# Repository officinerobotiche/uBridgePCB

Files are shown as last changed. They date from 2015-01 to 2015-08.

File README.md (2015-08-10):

# Officine Robotiche uBridge PCB
**The first DC motor board in 4cm X 4cm** - PCB boards for uBridge

This is a project in development by [Officine Robotiche] team.

###Join on open firmware project [uNAV.X](https://github.com/officinerobotiche/uNAV.X)!!!

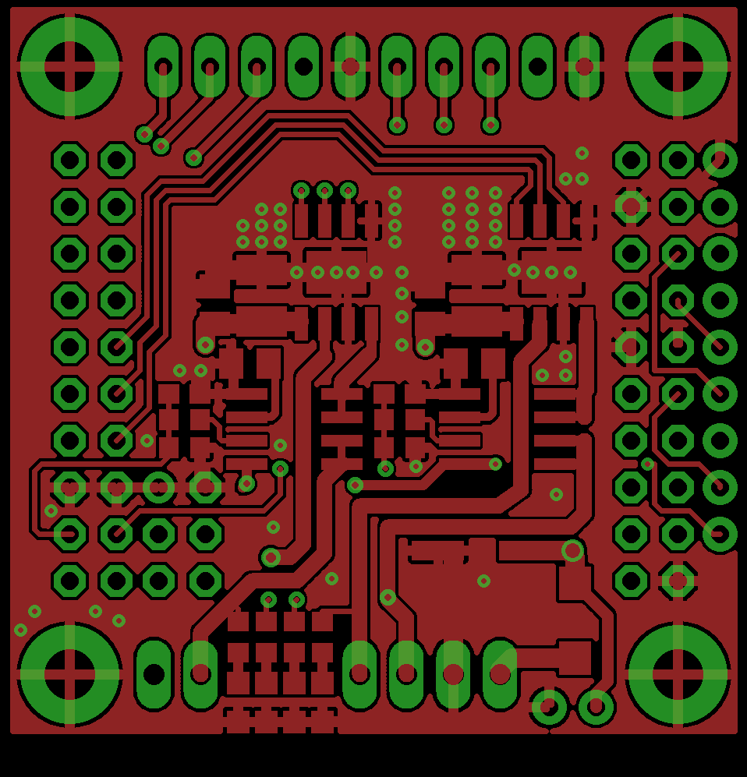
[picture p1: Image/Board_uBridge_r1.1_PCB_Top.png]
uBridge PCB Top

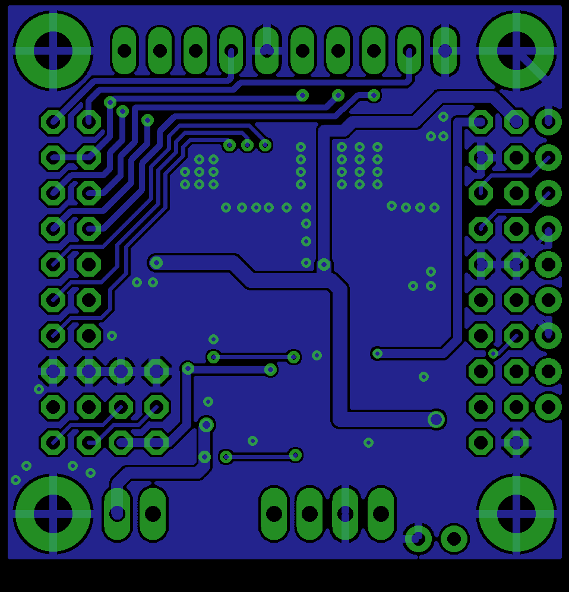
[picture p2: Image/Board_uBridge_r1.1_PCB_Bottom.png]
uBridge PCB Bottom

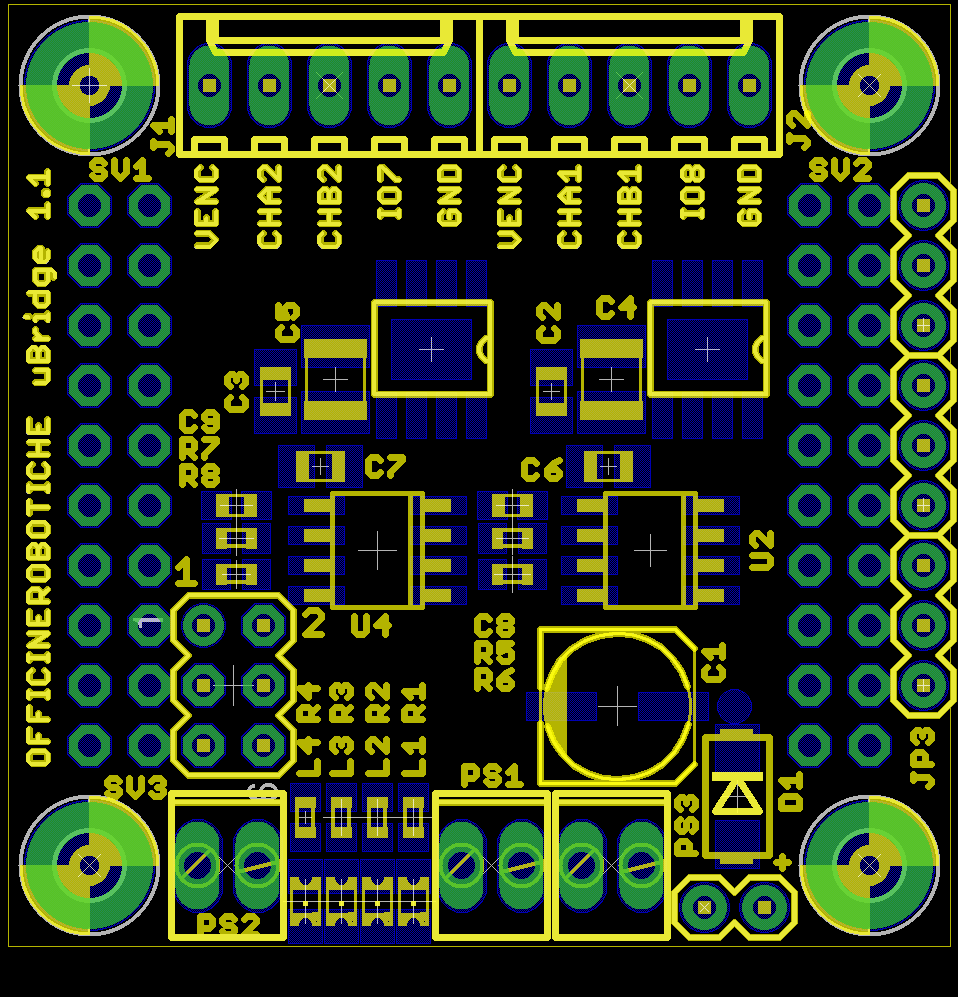
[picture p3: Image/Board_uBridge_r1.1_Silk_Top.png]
uBridge Silkscreen Top

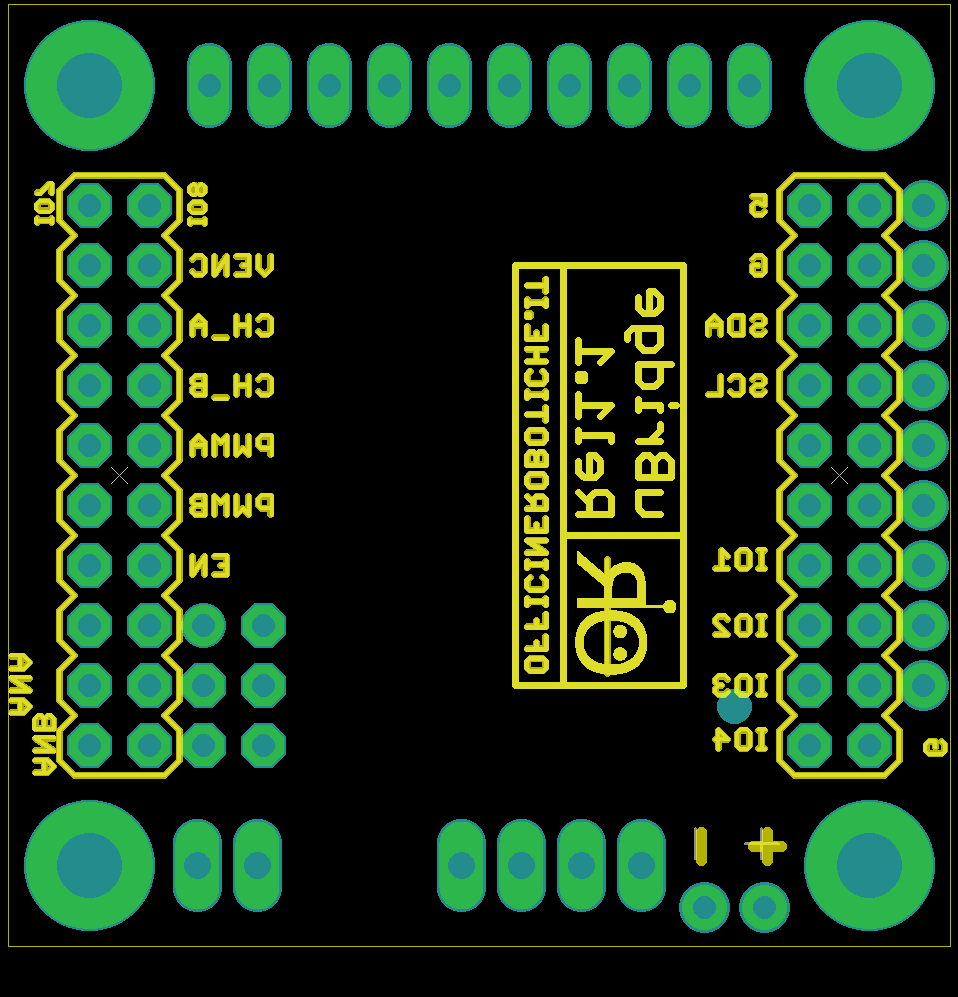
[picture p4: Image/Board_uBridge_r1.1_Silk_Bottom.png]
uBridge Silkscreen Bottom


# Hardware features
- 2 x A4950 Full-Bridge DMOS PWM Motor Driver
  - Up to 3,5A and 40V input ( limited at 23V if used with uNav )
  - Short circuit protected
  - Over Temperature protected
- 2 x ACS712 Hall Effect-Based Linear Current Sensor IC
  - ±5A Full-Scale input Range with 185mV/A variation
  - 2,5V output @ 0.0A
- 2 connector for Encoder with Gnd, Vcc, ChA, ChB, Chz signal.
- 4 LED on outupt of H-Bridge.
- Protection diode on input.
- size: 4cm x 4cm uNav stackable.
- Matrix board with holes 2.54mm compliant.

# Available Shields
- [uNav](https://github.com/officinerobotiche/uNAVPCB)
- [uMatrix](https://github.com/officinerobotiche/)

[Officine Robotiche]:http://www.officinerobotiche.it/
[Logo]:http://2014.officinerobotiche.it/wp-content/uploads/sites/4/2014/09/ORlogoSimpleSmall.png

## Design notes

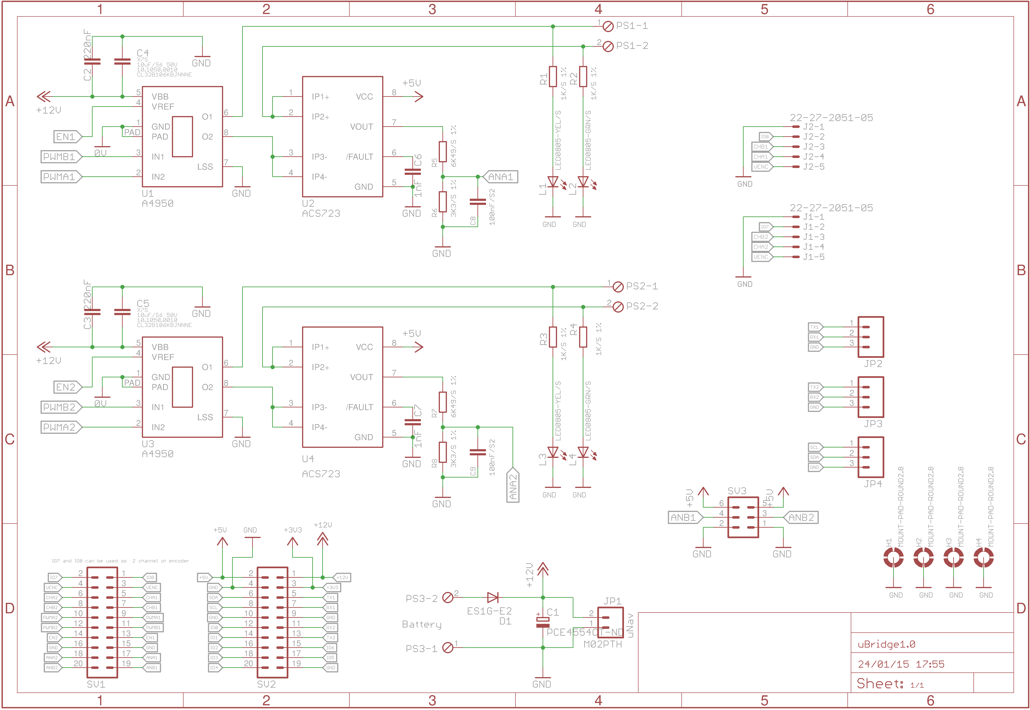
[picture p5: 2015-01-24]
Image/Scheme_uBridge_r1.png

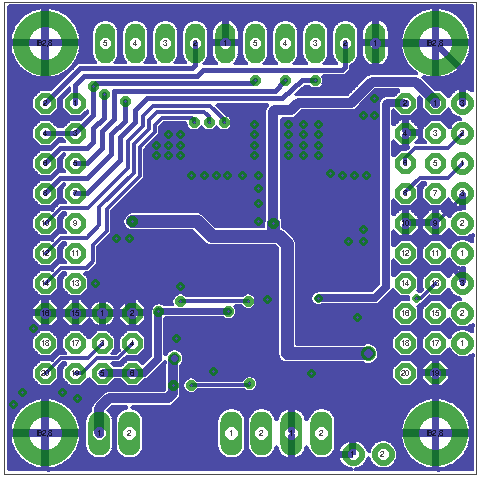
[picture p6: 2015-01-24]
Image/Board_uBridge_r1_PCB_Bottom.png

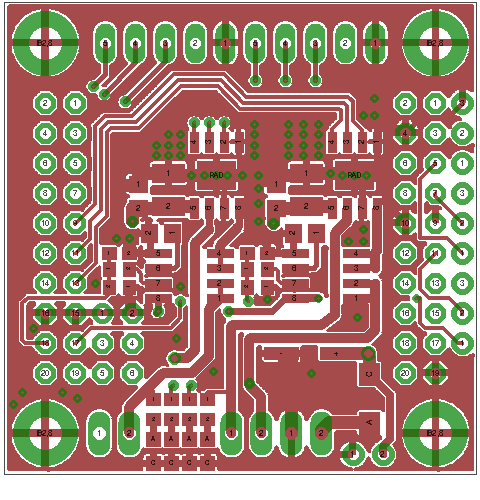
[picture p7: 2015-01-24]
Image/Board_uBridge_r1_PCB_Top.png

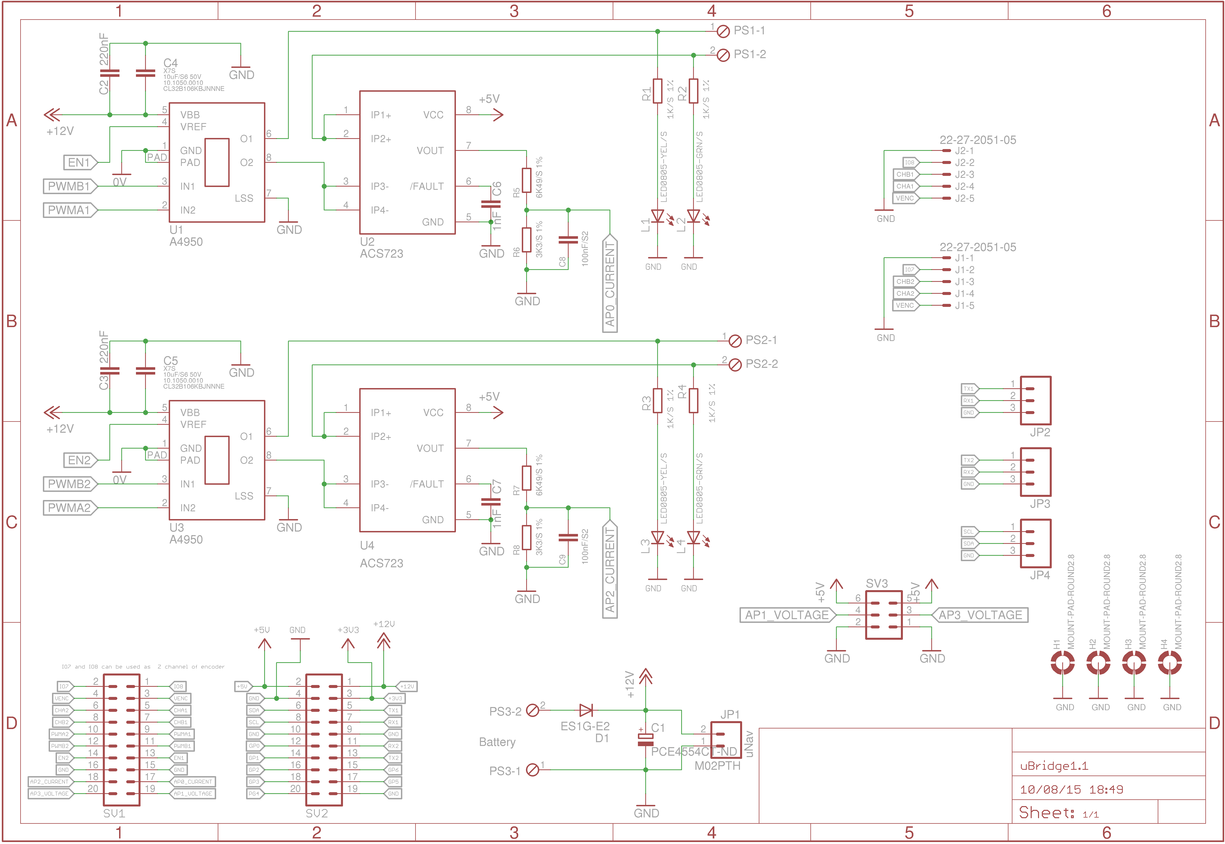
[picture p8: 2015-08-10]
Image/Scheme_uBridge_r1.1.png

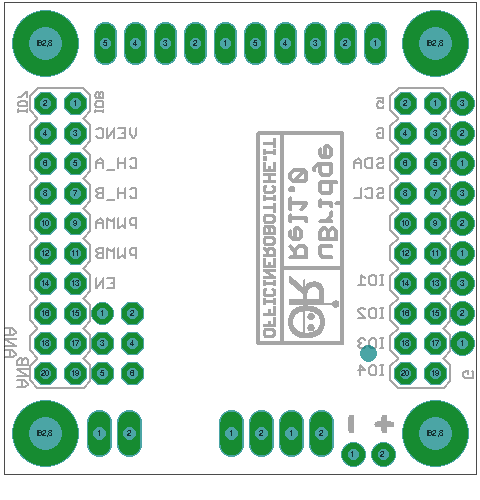
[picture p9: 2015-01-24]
Image/Board_uBridge_r1_Silk_Bottom.png

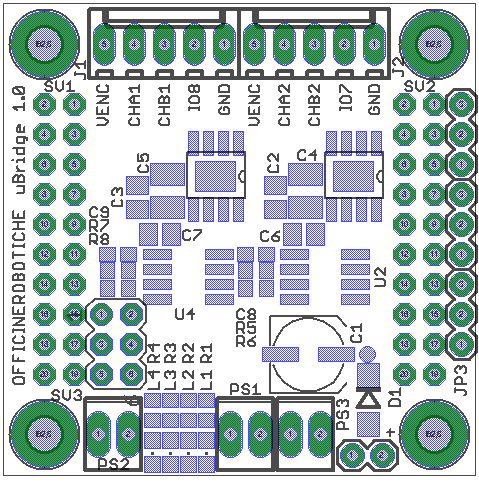
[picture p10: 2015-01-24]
Image/Board_uBridge_r1_Silk_Top.png

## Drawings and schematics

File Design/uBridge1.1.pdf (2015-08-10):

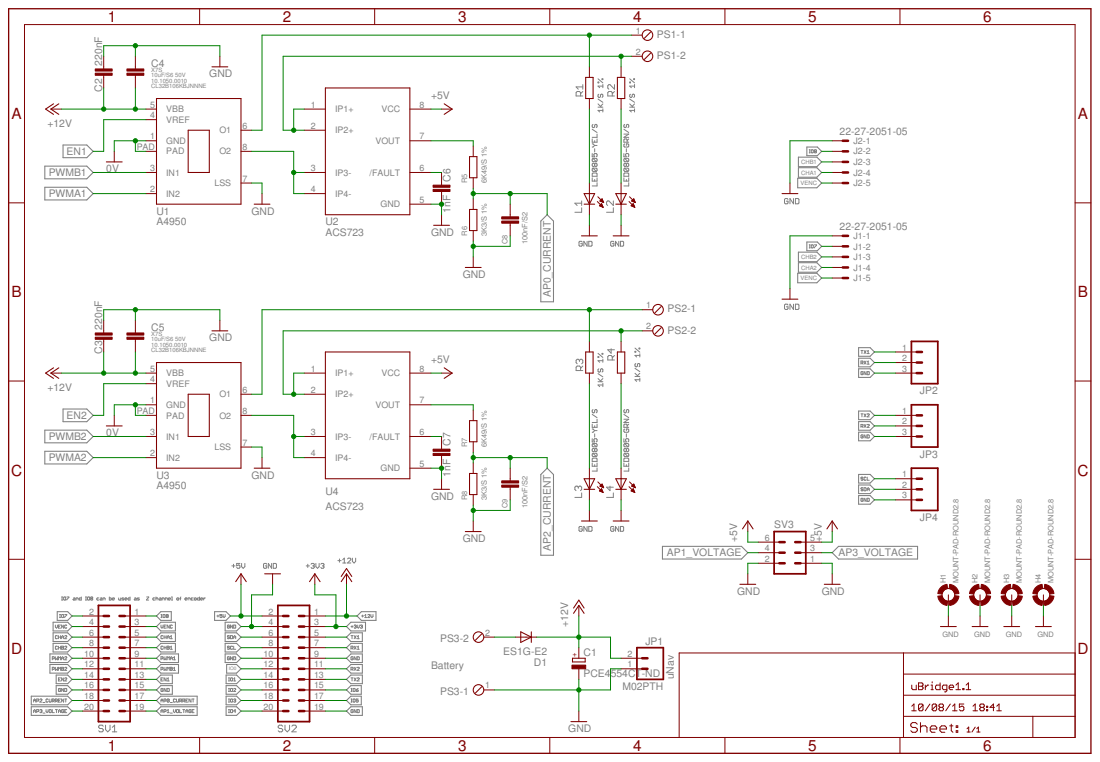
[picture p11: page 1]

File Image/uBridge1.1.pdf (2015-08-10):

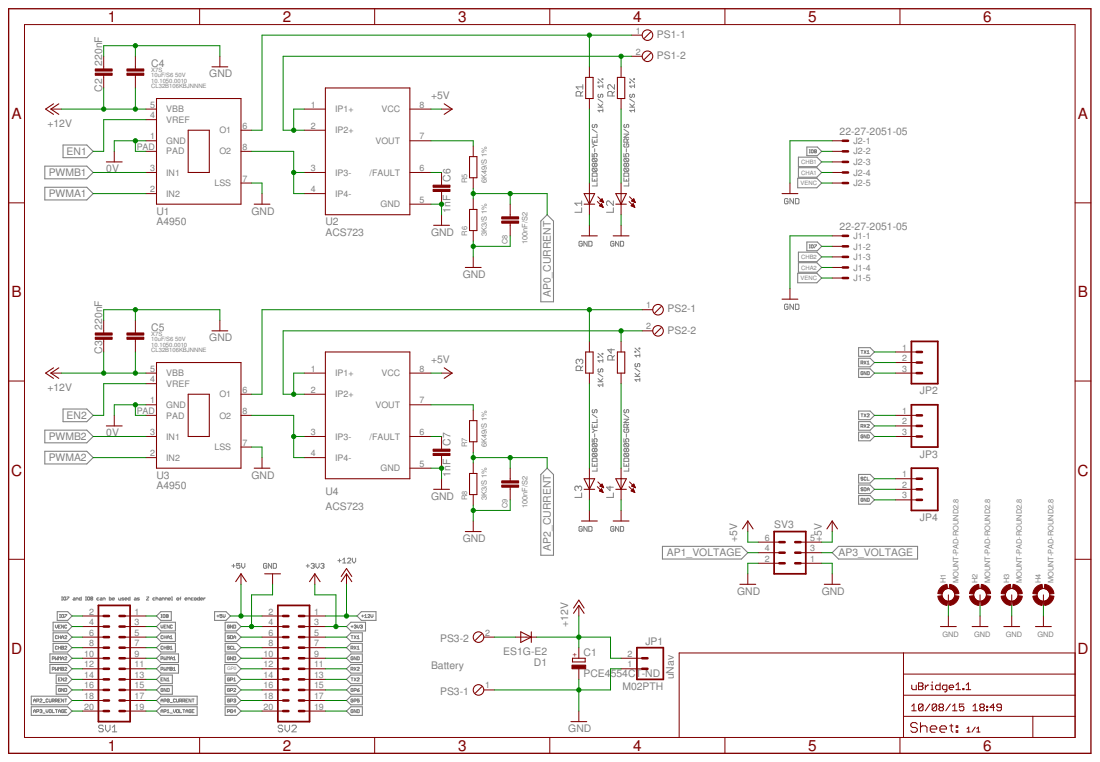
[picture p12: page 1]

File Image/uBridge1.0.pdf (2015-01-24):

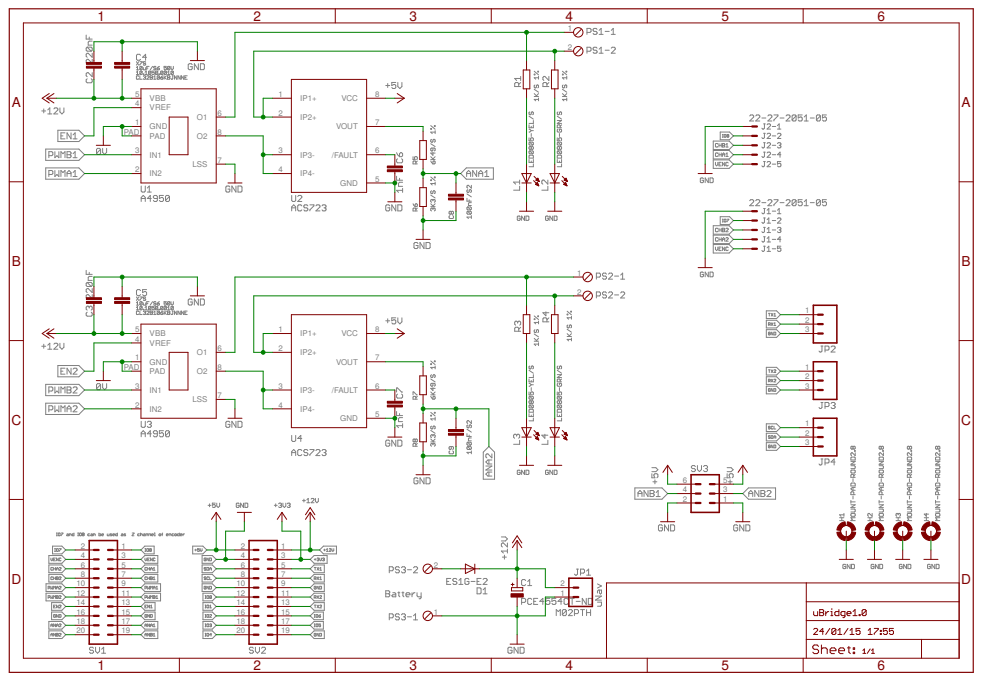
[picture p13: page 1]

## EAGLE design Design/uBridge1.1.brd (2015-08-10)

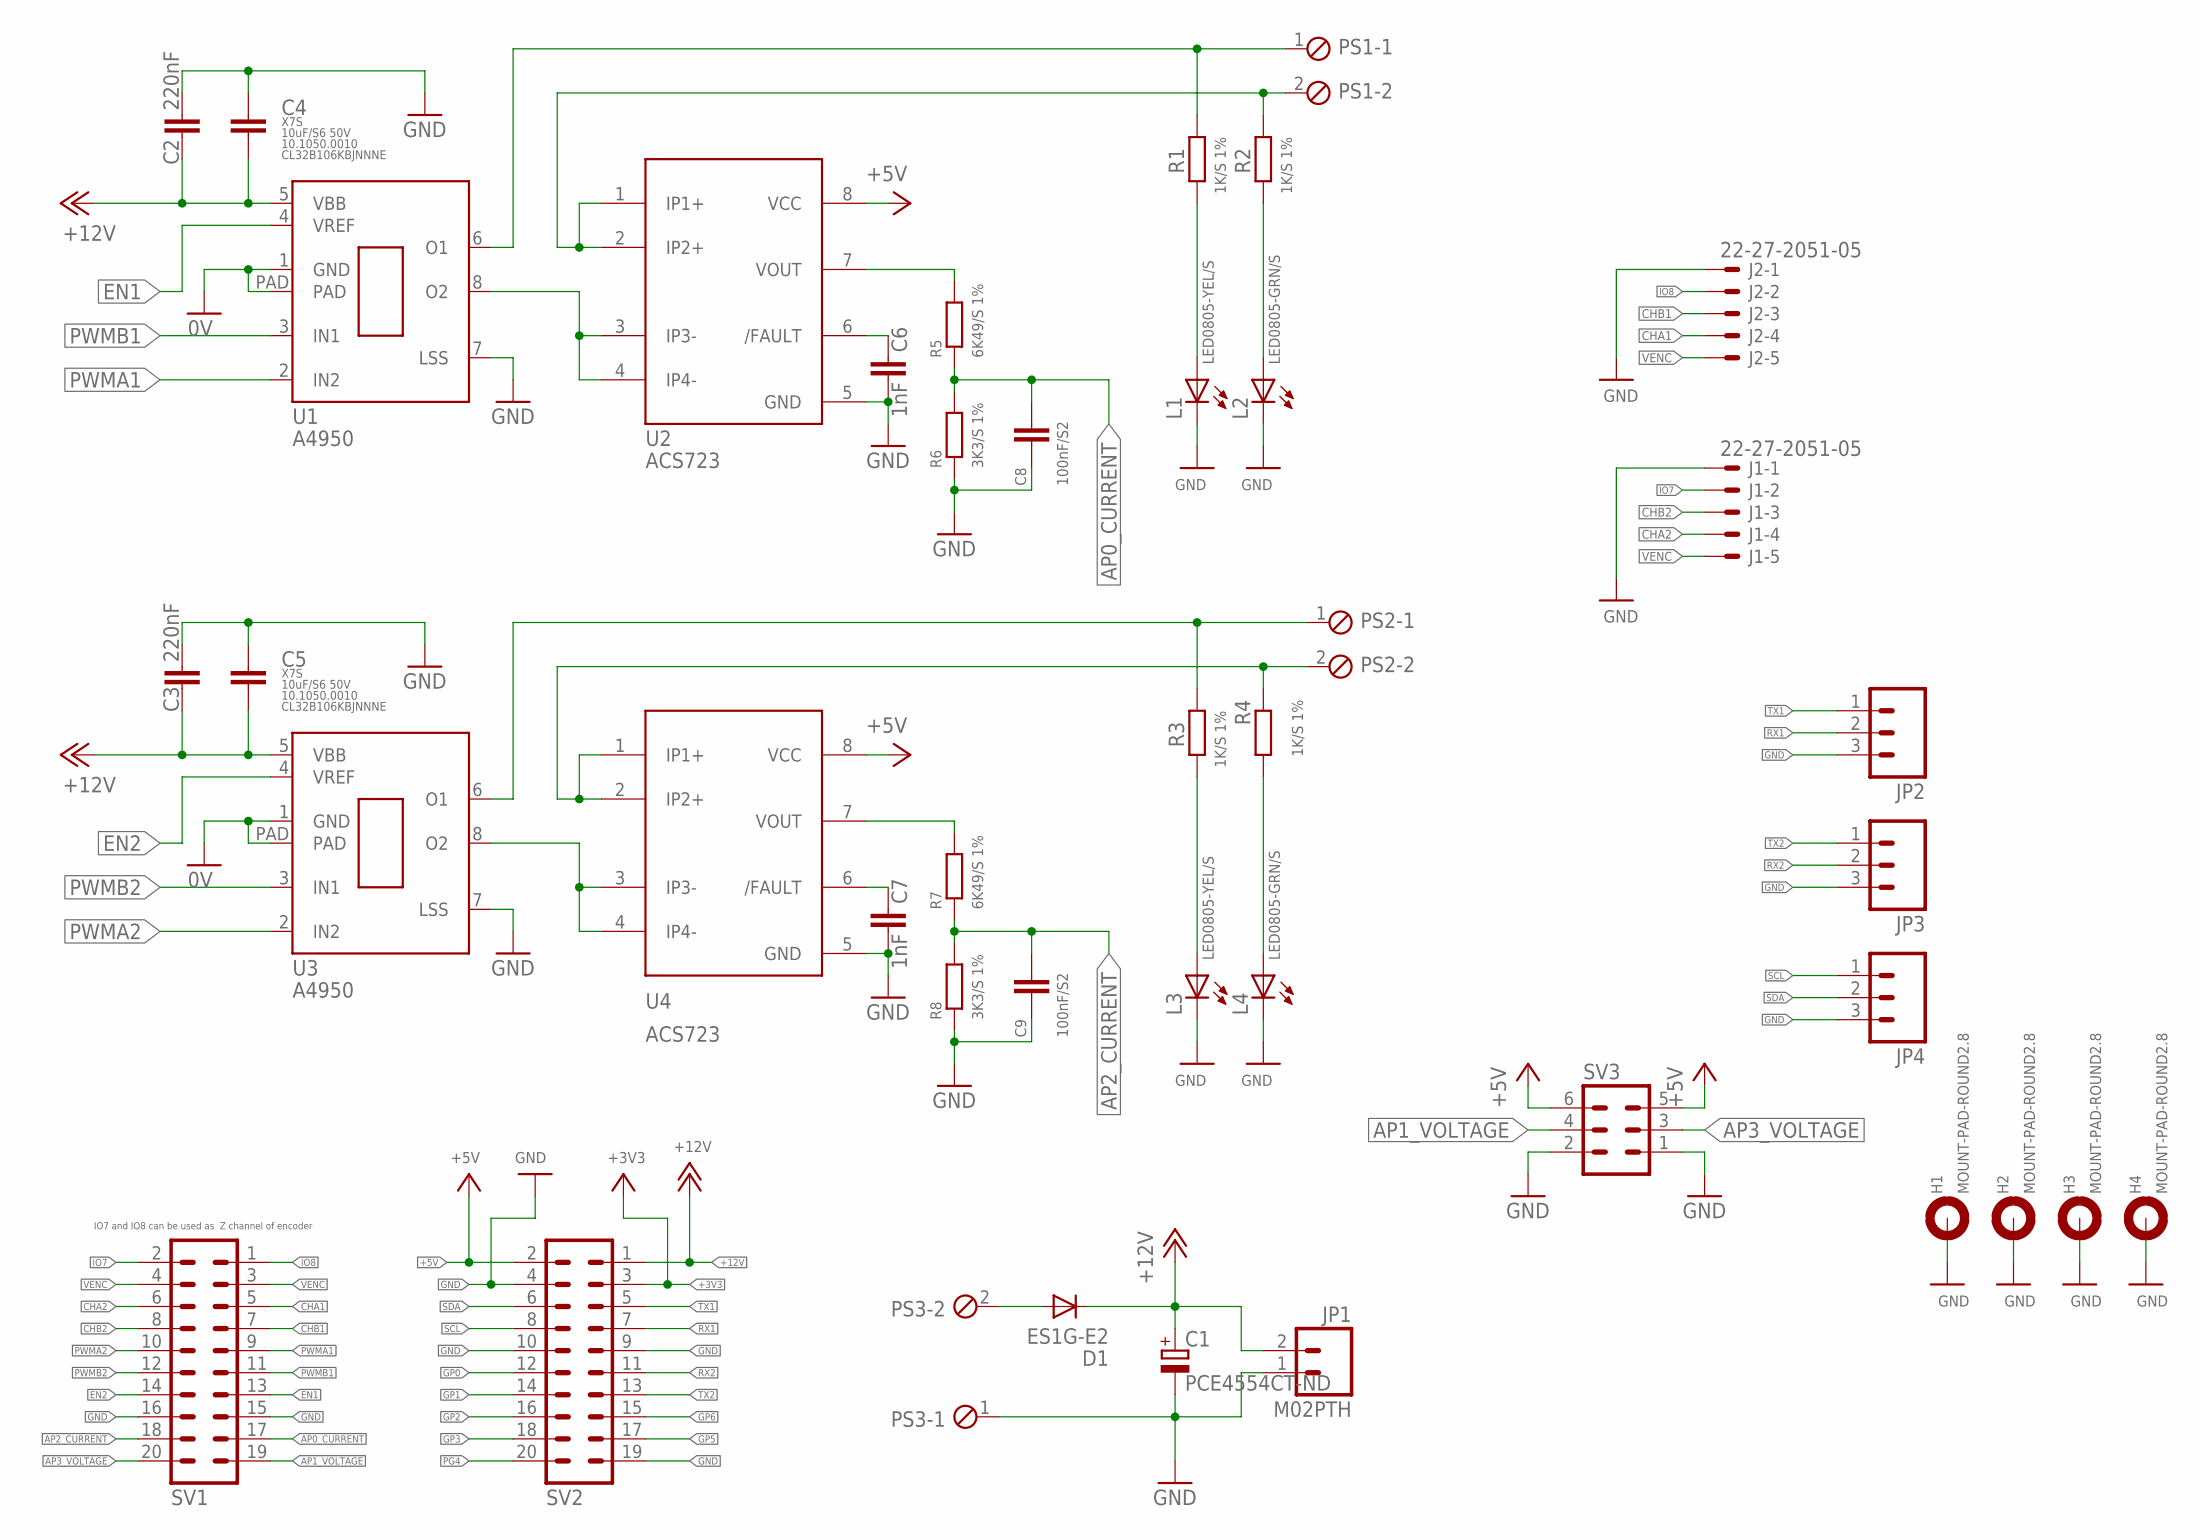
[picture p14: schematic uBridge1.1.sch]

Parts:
C1: PCE4554CT-ND; UD-6,3X7,7_NICHICON
C2, C3: 220nF; C0805K
C4, C5: 10uF/S6 50V; C3225
C6, C7: 1nF; C0805K
C8, C9: 100nF/S2; C0603
D1: ES1G-E2; DO214BA
H1, H2, H3, H4: MOUNT-PAD-ROUND2.8; 2,8-PAD
J1, J2: 22-27-2051-05; 6410-05
JP1: M02PTH; 1X02
JP2, JP3, JP4: M03PTH; 1X03
L1, L3: LED0805-YEL/S; CHIPLED_0805
L2, L4: LED0805-GRN/S; CHIPLED_0805
PS1, PS2, PS3: MPT2; 2POL254
R1, R2, R3, R4: 1K/S 1%; R0603
R5, R7: 6K49/S 1%; R0603
R6, R8: 3K3/S 1%; R0603
SV1, SV2: MA10-2
SV3: MA03-2
U1, U3: A4950; 8SOICN
U2, U4: ACS723; SO08

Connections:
+3V3: SV2.3
+5V: SV2.2, SV3.5, SV3.6, U2.8 (VCC), U4.8 (VCC)
+12V: C1.+, C2.2, C3.2, C4.2, C5.2, D1.C, JP1.2, SV2.1, U1.5 (VBB), U3.5 (VBB)
AP0_CURRENT: C8.1, R5.1, R6.2, SV1.17
AP1_VOLTAGE: SV1.19, SV3.4
AP2_CURRENT: C9.1, R7.1, R8.2, SV1.18
AP3_VOLTAGE: SV1.20, SV3.3
CHA1: J2.4, SV1.5
CHA2: J1.4, SV1.6
CHB1: J2.3, SV1.7
CHB2: J1.3, SV1.8
EN1: SV1.13, U1.4 (VREF)
EN2: SV1.14, U3.4 (VREF)
GND: C1.-, C2.1, C3.1, C4.1, C5.1, C6.2, C7.2, C8.2, C9.2, H1.B2,8, H2.B2,8, H3.B2,8, H4.B2,8, J1.1, J2.1, JP1.1, JP2.3, JP3.3, JP4.3, L1.C, L2.C, L3.C, L4.C, PS3.1, R6.1, R8.1, SV1.15, SV1.16, SV2.4, SV2.9, SV2.10, SV2.19, SV3.1, SV3.2, U1.1 (GND), U1.7 (LSS), U1.PAD, U2.5 (GND), U3.1 (GND), U3.7 (LSS), U3.PAD, U4.5 (GND)
GP0: SV2.12
GP1: SV2.14
GP2: SV2.16
GP3: SV2.18
GP5: SV2.17
GP6: SV2.15
IO7: J1.2, SV1.2
IO8: J2.2, SV1.1
unnamed: D1.A, PS3.2
unnamed: L1.A, R1.2
unnamed: L2.A, R2.2
unnamed: U1.8 (O2), U2.3 (IP3-), U2.4 (IP4-)
unnamed: R5.2, U2.7 (VOUT)
unnamed: U3.8 (O2), U4.3 (IP3-), U4.4 (IP4-)
unnamed: PS1.2, R2.1, U2.1 (IP1+), U2.2 (IP2+)
unnamed: PS2.2, R4.1, U4.1 (IP1+), U4.2 (IP2+)
unnamed: PS1.1, R1.1, U1.6 (O1)
unnamed: PS2.1, R3.1, U3.6 (O1)
unnamed: C6.1, U2.6 (/FAULT)
unnamed: C7.1, U4.6 (/FAULT)
unnamed: R7.2, U4.7 (VOUT)
PG4: SV2.20
PWMA1: SV1.9, U1.2 (IN2)
PWMA2: SV1.10, U3.2 (IN2)
PWMB1: SV1.11, U1.3 (IN1)
PWMB2: SV1.12, U3.3 (IN1)
RX1: JP2.2, SV2.7
RX2: JP3.2, SV2.11
SCL: JP4.1, SV2.8
SDA: JP4.2, SV2.6
TX1: JP2.1, SV2.5
TX2: JP3.1, SV2.13
VENC: J1.5, J2.5, SV1.3, SV1.4
VENC1-LD3: L3.A, R3.2
VENC2-LD4: L4.A, R4.2

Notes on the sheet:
IO7 and IO8 can be used as Z channel of encoder

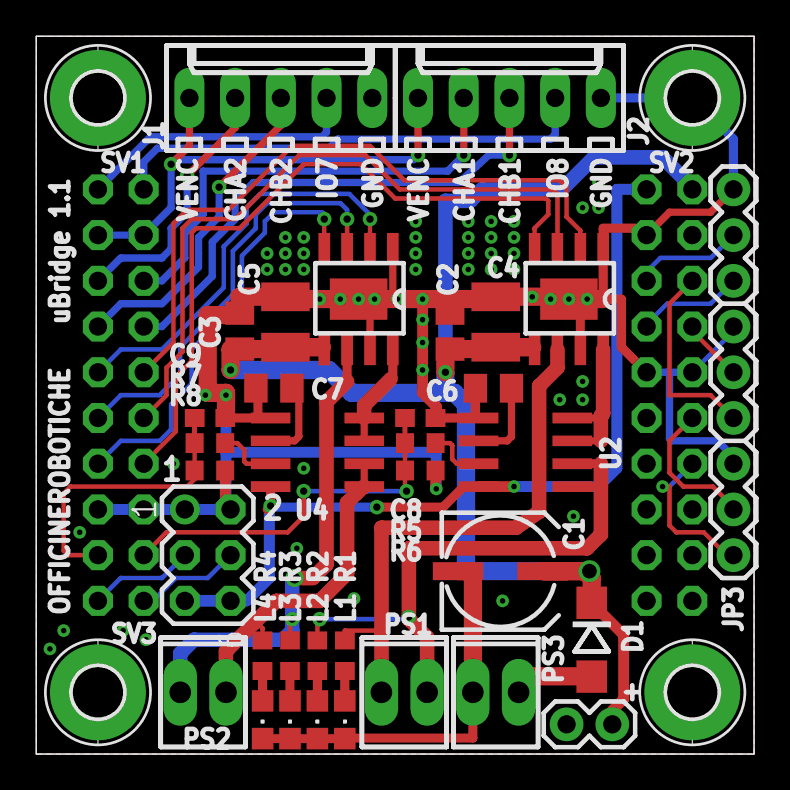
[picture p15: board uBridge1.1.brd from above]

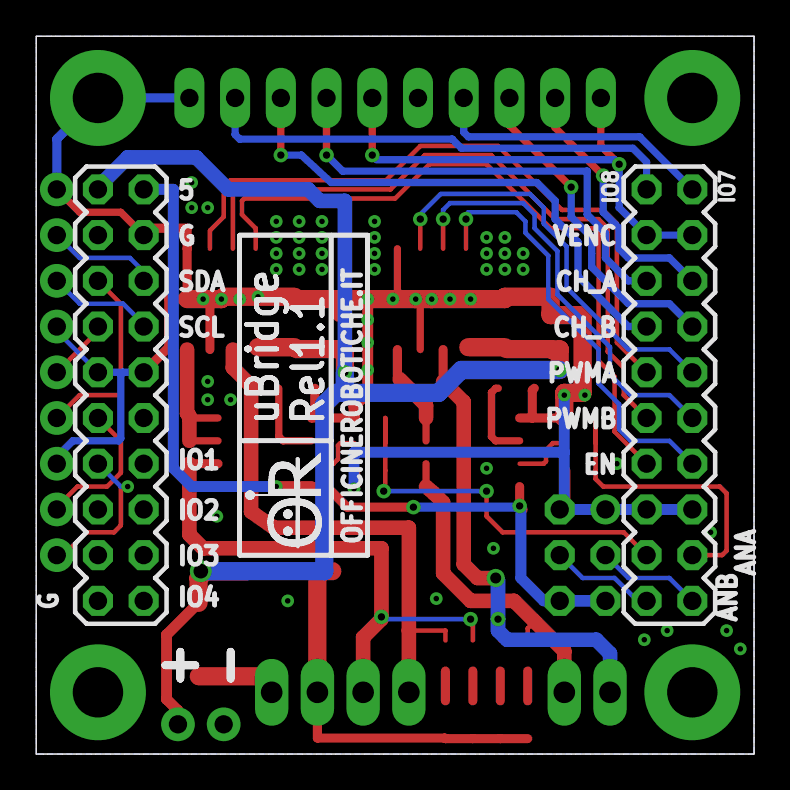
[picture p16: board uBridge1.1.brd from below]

Board: 2 copper layers, 39.9 x 39.9 mm, 42 parts (2 on the bottom side), 41 nets.

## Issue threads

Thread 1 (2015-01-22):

Encoder connector

rbonghi, 2015-01-22:
I would like to connect in the same board the motor encoders. I think is important have a single shield to connect all motors and all sensors.

Marnic, 2015-01-22:
ok, add to schematic

rbonghi, 2015-03-28:
Enlarge spaces between encoder connectors.

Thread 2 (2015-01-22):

Temperature sensor

rbonghi, 2015-01-22:
Can we put in same uBridge board a connector to measure temperature motor with a sensor temperature?
A sensor temperature similar to [LM35](http://www.ti.com/lit/ds/symlink/lm35.pdf)

Marnic, 2015-01-22:
ok, add to schematic an 1x3 pinhead for each motors with +5V, GND and data pin.
The data pin are connected to the ANA2 and ANB2 of the motor connector

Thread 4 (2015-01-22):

SATA style connecto for external bridge

katodo, 2015-01-22:
I wold use this board ( with a different mounting ) to connect uNAV to my RoboPonte Bridge with Sata cable ...

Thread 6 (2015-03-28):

Encoder pin SWAPPED on silkscreen

katodo, 2015-03-28:
On silkscreen of encoder connector name of signals are swapped :
CHA1 <-> CHA2
CHB1 <-> CHB2
IO7 <-> IO8

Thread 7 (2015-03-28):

Enlarge screw holes

rbonghi, 2015-03-28:
Enlarge holes for screw. The dimension is little bit small compare to M3 screw.

guiott, 2015-03-28:
I’ve encountered the same problem. The hole is 3mm but with the metal layer it’s reduced and no more enough for an M3 screw.
I’ve used an M2.5 screw that is much more better for the screw head size.
I’m afraid that if you really use an M3 screw you risk to touch some component with the head.
I suggest to reduce a bit the hole in order to be compatible with an M2.5 after the metal layer.

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

___________________
http://www.guiott.com/ <http://www.guiott.com/>

katodo, 2015-04-04:
Hole in PCB is 2,8mm diameter, designed for M2,5 screw with a little loose..

Myzhar, 2015-04-04:
It is not easy to find 2.5M screws. 3M are easier to use and find
Il 04/Apr/2015 12:29, "Katodo" <notifications@github.com> ha scritto:

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

rbonghi, 2015-04-13:
Yes @Myzhar !

@katodo I would like for unav and ubridge the holes for 3M screws.

katodo, 2015-04-13:
Ok, in new PCB version I change hole diameter if it's possible.

rbonghi, 2015-04-13:
:+1:

2015-04-13 14:53 GMT+02:00 Katodo <notifications@github.com>:

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

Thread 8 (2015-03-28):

Switch for Power PIN

rbonghi, 2015-03-28:
In the power PIN I would like to have a switch to select direct power supply for uNav or different source.

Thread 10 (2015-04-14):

Add a Voltage bridge sensor

rbonghi, 2015-04-14:
In unav schematic we have two Analog pin free, IO2 and IO1 (AN6 and AN7).

I think for a good low level control for torque, velocity and position, to add a voltage sensor for measure tension on motors.

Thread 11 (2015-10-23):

H-bridge hangs out with current lesser than 2A

Myzhar, 2015-10-23:
According to tests made using E192.12.18 motors, the H-Bridge hangs out for current lesser than the maximum 3A current.

@Marnic has verified that this fact does not happen with adding an R_sense on PIN 7 of the Allegro A4950.

On the datasheet, pg 7,  (http://www.allegromicro.com/~/media/Files/Datasheets/A4950-Datasheet.ashx?la=en) there are more information about a good configuration of the PCB to suite the R_sense

katodo, 2015-10-29:
...I've found this solution:
https://drive.google.com/open?id=0B5F6KPas919hUXdoQ251cFhSQlE

Resolution step:
- lift up pin number 7 of each A4950
- Solder a 0,1 Ohm resistor on GND pin of  C4 and C5... place it on top of A4950, from GND capacitor pin and A4950 7 pin direction.
- solder resistor and pin number 7 with a small part of wire.
- ...test it :)

Myzhar, 2015-10-29:
Ok. According to datasheet 0.1 ohm is the right resistor value to allow maximum current since V_en is 3.3V.
I'm going to test it and close the issue if everything is fine

Myzhar, 2015-11-05:
From the test made using motors that sink more than 2.5A of current I verified that 0.1 ohm is a value too low, causing the uBridge to work choppy when the motor is under heavy effort.

@Marnic  suggests to limit the current to 2A or 2.5A

We should now test these values:
Rs = 0.165 ohm to limit to 2A
Rs = 0.132 ohm to limit to 2.5A

calculated according to the formula
Rs = Vref /(10*I_max)
at pg 5 of the datasheet, with Vref = 3.3V

@katodo which values can be found as "real" resistors?

katodo, 2015-11-05:
http://www.google.com/url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

Myzhar, 2015-11-05:
I ordered
0.15 ohm 1W 1%
and
0.16 ohm 500mW 1%

I'm going to make the first test using 0.15 ohm... then I will change to 0.16 ohm, but only if the issue has not been solved using 0.15 ohm

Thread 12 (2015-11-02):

Wrong diode usage

katodo, 2015-11-02:
Input Diode D1 is placed before A4950 power path (Vbb)... it would be necessary a 7A diode or a mosfet based voltage reverse polarity protection circuit like :
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

For Rev 1.x PCB there are 2 possible workaround:
- Remove D1 and bypass it with a 0 ohm resistor. It's very simple but... reverse polarity will be destroy uBridge, uNav and other devide connected!!
- Perform a complex ( but less destructive ) patch like this gallery:
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

Myzhar, 2015-11-05:
This solution is working. So I suggest to keep the current diode to protect the uNav and correct the schematic to replicate this solution

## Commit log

2015-01-13 First commit / temporary repository files / I must organize them
    [Master10.brd, Master10.sch, MasterAlternativo10.brd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]
2015-01-22 updated with encoder and temperature connectors
    [uBridge2.0.brd, uBridge2.0.sch]
2015-01-22 add SATA connector
    [uBridge2.0.brd, uBridge2.0.sch]
2015-01-24 obsolete file removed
    [Master10.brd, Master10.sch, MasterAlternativo10.brd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]
2015-01-24 Final release of uBridge
    [uBridge1.0.BottomCream.gbr, uBridge1.0.Layer_Bottom.gbr, uBridge1.0.Layer_Top.gbr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]
2015-01-26 Final revision
    [uBridge1.0.BottomCream.gbr, uBridge1.0.Layer_Bottom.gbr, uBridge1.0.Layer_Top.gbr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]
2015-08-10 Update some signal name and wrong silkscreen on Encoder connector.
    [uBridge1.0.BottomCream.gbr, uBridge1.0.Layer_Bottom.gbr, uBridge1.0.Layer_Top.gbr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]
2015-08-10 Solved little issue on label name and release file name.
    [uBridge1.1.brd, uBridge1.1.sch]

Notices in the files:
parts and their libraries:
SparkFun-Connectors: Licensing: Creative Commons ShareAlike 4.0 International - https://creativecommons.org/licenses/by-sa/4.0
